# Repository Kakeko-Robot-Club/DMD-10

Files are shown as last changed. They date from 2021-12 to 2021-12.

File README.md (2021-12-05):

# DMD-10
ディスクリート部品によるDCブラシモータドライバ
## 目次
 - [仕様](#仕様)
 - [変更履歴](#変更履歴)
 - [発注](#発注)
 - [部品実装](#部品実装)
 - [使い方](#使い方)
## 仕様
### 絶対最大定格
| 項目 | 記号 | Max | 単位 | 
| --- | :---: | :---: | :--: |
| モータ出力電流(rms) | I<sub>OUT</sub> | 10 | A | 
| モータ出力電流(peak)  | I<sub>OUT_PEAK</sub> | 17 | A | 
| モータ電源電圧 | V<sub>DD</sub> | 0~16 | V | 
| ロジック入力電圧 | V<sub>IN</sub> | -6~23 | V | 
| 保存温度 | T<sub>S</sub> | -55~125 | ℃ | 
### 電気的特性・動作範囲
| 項目 | 記号 | Min | Typ. | Max | 単位 | コンディション | 
| --- | :---: | :-: | :--: | :-: | :--: | --- |
| モータ電源電圧 | V<sub>DD</sub>  | 6 | - | 16  | V | | 
| ロジック入力電圧(High)| V<sub>IH</sub>  | 3.6 | - | 20  | V | | 
| ロジック入力電圧(Low) | V<sub>IL</sub>  | 0 | - | 1.4 | V | | 
| ロジックPWM周波数 | f<sub>IN</sub>  | - | - | 27  | kHz | | 
| ロジック入力電流 | I<sub>IN</sub>  | - | 10 | - | mA | V<sub>IN</sub>=5V | 
### その他
| 項目 | 記号 | Min | Typ. | Max | 単位 | 備考 | 
| --- | :---: | :-: | :--: | :-: | :--: | --- |
| 基板サイズ(縦) | | - | 55 | - | mm | | 
| 基板サイズ(横) | | - | 60 | - | mm | | 
| 取り付け穴サイズ | | - | 3.2  | - | mm | M3ネジ用 | 
| 取り付け穴ピッチ(縦)  | | - | 46 | - | mm | | 
| 取り付け穴ピッチ(横)  | | - | 35 | - | mm | | 
### 図
 - [回路図](https://github.com/Kakeko-Robot-Club/DMD-10/blob/main/preview/schematic.pdf)
 - [基板外形図](https://github.com/Kakeko-Robot-Club/DMD-10/blob/main/preview/pcb.pdf)
## 変更履歴
 - Rev. A
	 - 初版(GitHubには未掲載)
 - Rev. B
	 - 部品リファレンス番号の振り直し
## 発注
 - 発注手順は[Elecrow](https://www.elecrow.com/pcb-manufacturing.html)に発注する際の手順を示しているため、その他の業者に発注する際は各業者の指示に従うこと。
 - 下の1～4の手順が難しい場合、このリポジトリの中にあるgerberフォルダの中のファイルを使用しても良い。ただし、手順1が行えないため注意。
 - 設定はKiCad v5系を元にしているため、その他のバージョンの場合は同等の設定にすること。
1. KiCadのPcbnewを用いて基板型番の下にある週番号を振り直す。
	 - この手順は省略できるが、製造時期を明確にするために行ったほうが良い。
2. Pcbnewから、ファイル→プロットと進み、出てきた画面で次のように設定をし、「製造ファイル出力」を押す。
	 - 出力フォーマット: ガーバー
	 - 出力ディレクトリ: gerberなど分かりやすいもの
	 - 含まれるレイヤ
		 - [x] F.Cu
		 - [x] B.Cu
		 - [x] F.SilkS
		 - [x] B.SilkS
		 - [x] F.Mask
		 - [x] B.Mask
		 - [x] Edge.Cuts
		 - その他はチェックを外す
	 - 全般オプション
		 - [x] フットプリントの定数をプロット
		 - [x] フットプリントのリファレンスをプロット
		 - [x] 基板外形レイヤーのデータを他のレイヤーから除外
		 - [x] シルクからパッドを除外
		 - その他はチェックを外す
		 - デフォルトの線幅: 0.1mm
	 - ガーバーオプション
		 - [x] Protelの拡張子を使用
		 - [x] シルクをレジストで抜く
		 - [x] ネットリスト属性を含む
		 - その他はチェックを外す
		 - 座標フォーマット: 4.6, 単位 mm
3. 製造ファイル出力ボタンの右の方にある、「ドリルファイルを生成...」ボタンから、次のように設定し、「ドリルファイルを生成」を押す。
	 - 出力フォルダ: 製造ファイル出力で設定したものと同じもの
	 - ドリルファイルフォーマット: Excellon
		 - チェックはすべて外す
		 - 長円穴ドリルモードは「routeコマンドを使用」にチェック
	 - マップファイルフォーマット: ガーバー
	 - ドリル原点: 絶対位置
	 - ドリル単位: mm
	 - ゼロの扱い: 後方ゼロ省略
4. 基板プロジェクトフォルダの中のフォルダ、または自分で設定したフォルダの中に生成したファイル群があるので、次のようにリネームする。
	 - DMD-10-Edge.Cuts.gm1のみ、拡張子がgmlに変わっているため注意

	| 元ファイル名         | リネーム後      | 
	| -------------------- | --------------- | 
	| DMD-10-B.Cu.gbl      | DMD-10.gbl      | 
	| DMD-10-B.Mask.gbs    | DMD-10.gbs      | 
	| DMD-10-B.SilkS.gbo   | DMD-10.gbo      | 
	| DMD-10-Edge.Cuts.gm1 | DMD-10.gml      | 
	| DMD-10-F.Cu.gtl      | DMD-10.gtl      | 
	| DMD-10-F.Mask.gts    | DMD-10.gts      | 
	| DMD-10-F.SilkS.gto   | DMD-10.gto      | 
	| DMD-10-NPTH.drl      | DMD-10-NPTH.txt | 
	| DMD-10-PTH.drl       | DMD-10-PTH.txt  | 
5. ファイルをZIPファイルに圧縮する。
6. [Elecrow](https://www.elecrow.com/pcb-manufacturing.html)にZIPファイルをアップロードし、次のような設定で発注する。
	 - Elecrowにログインしておくこと。

	| 項目                 | 設定             | 備考                                                   | 
	| -------------------- | :--------------: | ------------------------------------------------------ | 
	| Layer                | 2 layers         | 変更しないこと。                                       | 
	| Dimensions           | 60 x 55          | 変更しないこと。                                       | 
	| PCB Qty              | 必要枚数を設定   | 10枚までは安い。設定より少し多めに届くことが多い。     | 
	| Different PCB Design | 1                | 変更しないこと。                                       | 
	| PCB Thickness        | 1.6              | 薄くできるが非推奨。厚くすると高くなる。               | 
	| PCB Color            | 基板色を設定     | 一部の色は高い。                                       | 
	| Surface Finish       | HASL             | 鉛フリーや金メッキなども指定できるが高くなる。         | 
	| Castellated Hole     | No               | 変更しないこと。                                       | 
	| Copper Weight        | 1oz              | 2ozは基板銅箔が厚くなるが高くなる。                    | 
	| PCB Stencil          | No               | ステンシルは表面実装部品のリフロー半田に使うので不要。 | 
	| Production Time      | 4-7 working days | Rushなどにしてもそこまで早くならない。                 | 
	| Country              | Japan            | 配送先の国なので日本を選択。                           | 
	| Shipping Cost        | Sagawa           | 一番安いものを選んでおけばよい。                       | 
## 部品実装
 - 部品リスト
	| リファレンス | 部品                | 秋月電子                                                                                                                        | 代替品情報                                              | 
	| ------------ | ------------------- | ------------------------------------------------------------------------------------------------------------------------------- | ------------------------------------------------------- | 
	| D1～D4       | SBM1045VSS          | [I-15642](https://akizukidenshi.com/catalog/g/gI-15642/)                                                                        | I<sub>F</sub>>10A, V<sub>R</sub>>16V                    | 
	| J1～J4       | PCB-20(632F)        | [C-05115](https://akizukidenshi.com/catalog/g/gC-05115/)                                                                        | 15A以上流せるもの, できるだけ金属面積が広いもの         | 
	| J5           | PH-1x40RG(2)        | [C-01627](https://akizukidenshi.com/catalog/g/gC-01627/)                                                                        | 2.54mmピッチ, L字                                       | 
	| Q1, Q2       | MTA100N10KRI3       | 1個: [I-15846](https://akizukidenshi.com/catalog/g/gI-15846/)<br>10個: [I-15847](https://akizukidenshi.com/catalog/g/gI-15847/) | TO-251, Nch, I<sub>D</sub>>2A, V<sub>GS(th)</sub><4V    | 
	| Q3, Q5       | IRFU5505PBF         | [I-06021](https://akizukidenshi.com/catalog/g/gI-06021/)                                                                        | TO-251, Pch, I<sub>D</sub><-15A, V<sub>GS(th)</sub>>-4V | 
	| Q4, Q6       | IRLU3410PBF         | [I-06025](https://akizukidenshi.com/catalog/g/gI-06025/)                                                                        | TO-251, Nch, I<sub>D</sub>>15A, V<sub>GS(th)</sub><4V   | 
	| R1～R4       | 300Ωカーボン抵抗   | [R-07811](https://akizukidenshi.com/catalog/g/gR-07811/)                                                                        |                                                         | 
	| R5, R6       | 10kΩカーボン抵抗   | [R-07838](https://akizukidenshi.com/catalog/g/gR-07838/)                                                                        |                                                         | 
	| R7～R10      | 10Ωカーボン抵抗    | [R-07795](https://akizukidenshi.com/catalog/g/gR-07795/)                                                                        |                                                         | 
	| RN1          | 1kΩ 4素子集合抵抗  | [R-14225](https://akizukidenshi.com/catalog/g/gR-14225/)                                                                        |                                                         | 
	| RN2          | 10kΩ 4素子集合抵抗 | [R-11909](https://akizukidenshi.com/catalog/g/gR-11909/)                                                                        |                                                         | 
	| U1, U2       | UPC817CG-D04-T      | [I-16090](https://akizukidenshi.com/catalog/g/gI-16090/)                                                                        | PC817系フォトカプラ                                     | 
 - 注意点
	 - 抵抗やダイオードは縦取り付けになるよう、リードを曲げること。
	 - リードを曲げた抵抗を取り付ける際、基板から浮かないように取り付けること。
		 - 浮いている場合、抵抗が左右に曲がりやすくなり、ショートの原因になるため注意。
	 - 放熱のため、FETの頭の部分の半田付けは確実に行う。
		 - ランドが広いため、大出力の半田ごてを用いたほうが良い。
	 - ネジ端子はよく温めないと半田が流れないため、やけどに注意。
	 - 言うまでもなく、部品の向き・極性の間違い、定数の間違いに注意する。
## 使い方
1. 次のように接続する。
	| 端子      | リファレンス | 接続先             | 
	| --------- | ------------ | ------------------ | 
	| POWER IN  | J2           | モータ電源プラス   | 
	| POWER GND | J3           | モータ電源マイナス | 
	| MOTOR OUT | J1, J4       | DCブラシモータ     | 
	| IN1       | J5           | マイコン等出力端子 | 
	| IN2       | J5           | マイコン等出力端子 | 
	| GND       | J5           | マイコン等グランド | 
2. マイコン等から次の表に従い、IN1・IN2に信号を出力する。
	| IN2 | IN1 | J4  | J1  | モータ   | 
	| --- | --- | --- | --- | -------- | 
	| 0   | 0   | 1   | 1   | ブレーキ | 
	| 0   | 1   | 1   | 0   | 回転     | 
	| 1   | 0   | 0   | 1   | 逆回転   | 
	| 1   | 1   | 0   | 0   | ブレーキ | 
  
	*IN1・IN2欄は入力状態、J1・J4欄は出力状態、モータ欄は出力状態によるモータの状態を表す。  
	*IN1・IN2については0をV<sub>IL</sub>、1をV<sub>IH</sub>（PWM入力含む）に従うものとする。  
	*J1・J4については0を0V、1をV<sub>DD</sub>に従うものとする。

### 使用上の注意
 - 各端子をショートさせないこと。
 - 熱がこもるような狭い空間で使用しないこと。
 - 定格を超えての使用をしないこと。
 - 異常発熱がある場合は使用しないこと。

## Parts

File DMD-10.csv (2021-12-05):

Reference | Value | Footprint | Datasheet
J3 | Conn_01x04 | Connector_PinHeader_2.54mm:PinHeader_1x04_P2.54mm_Horizontal | ~
U1 | PC817 | Package_DIP:DIP-4_W7.62mm | http://www.soselectronic.cz/a_info/resource/d/pc817.pdf
U2 | PC817 | Package_DIP:DIP-4_W7.62mm | http://www.soselectronic.cz/a_info/resource/d/pc817.pdf
R1 | 380 | Resistor_THT:R_Axial_DIN0204_L3.6mm_D1.6mm_P2.54mm_Vertical | ~
R2 | 380 | Resistor_THT:R_Axial_DIN0204_L3.6mm_D1.6mm_P2.54mm_Vertical | ~
R5 | 300 | Resistor_THT:R_Axial_DIN0204_L3.6mm_D1.6mm_P2.54mm_Vertical | ~
R6 | 300 | Resistor_THT:R_Axial_DIN0204_L3.6mm_D1.6mm_P2.54mm_Vertical | ~
Q1 | MTA100N10KRI3 | Package_TO_SOT_THT:TO-251-3-1EP_Horizontal_TabDown | ~
Q2 | MTA100N10KRI3 | Package_TO_SOT_THT:TO-251-3-1EP_Horizontal_TabDown | ~
R7 | 10k | Resistor_THT:R_Axial_DIN0204_L3.6mm_D1.6mm_P2.54mm_Vertical | ~
R8 | 10k | Resistor_THT:R_Axial_DIN0204_L3.6mm_D1.6mm_P2.54mm_Vertical | ~
Q4 | IRLU3410PBF | Package_TO_SOT_THT:TO-251-3-1EP_Horizontal_TabDown | ~
Q6 | IRLU3410PBF | Package_TO_SOT_THT:TO-251-3-1EP_Horizontal_TabDown | ~
R11 | 10 | Resistor_THT:R_Axial_DIN0204_L3.6mm_D1.6mm_P2.54mm_Vertical | ~
R12 | 10 | Resistor_THT:R_Axial_DIN0204_L3.6mm_D1.6mm_P2.54mm_Vertical | ~
Q3 | IRFU5505PBF | Package_TO_SOT_THT:TO-251-3-1EP_Horizontal_TabDown | ~
Q5 | IRFU5505PBF | Package_TO_SOT_THT:TO-251-3-1EP_Horizontal_TabDown | ~
R13 | 10 | Resistor_THT:R_Axial_DIN0204_L3.6mm_D1.6mm_P2.54mm_Vertical | ~
R14 | 10 | Resistor_THT:R_Axial_DIN0204_L3.6mm_D1.6mm_P2.54mm_Vertical | ~
D1 | SBM1045VSS | Diode_THT:D_DO-201AD_P3.81mm_Vertical_AnodeUp | ~
D2 | SBM1045VSS | Diode_THT:D_DO-201AD_P3.81mm_Vertical_AnodeUp | ~
D3 | SBM1045VSS | Diode_THT:D_DO-201AD_P3.81mm_Vertical_AnodeUp | ~
D4 | SBM1045VSS | Diode_THT:D_DO-201AD_P3.81mm_Vertical_AnodeUp | ~
J4 | Conn_01x01 | PCB-20(632)F:DIP-6_W7.62mm | ~
J5 | Conn_01x01 | PCB-20(632)F:DIP-6_W7.62mm | ~
J2 | Conn_01x01 | PCB-20(632)F:DIP-6_W7.62mm | ~
J1 | Conn_01x01 | PCB-20(632)F:DIP-6_W7.62mm | ~
RN1 | 10k | Resistor_THT:R_Array_SIP5 | http://www.vishay.com/docs/31509/csc.pdf
RN2 | 1k | Resistor_THT:R_Array_SIP5 | http://www.vishay.com/docs/31509/csc.pdf

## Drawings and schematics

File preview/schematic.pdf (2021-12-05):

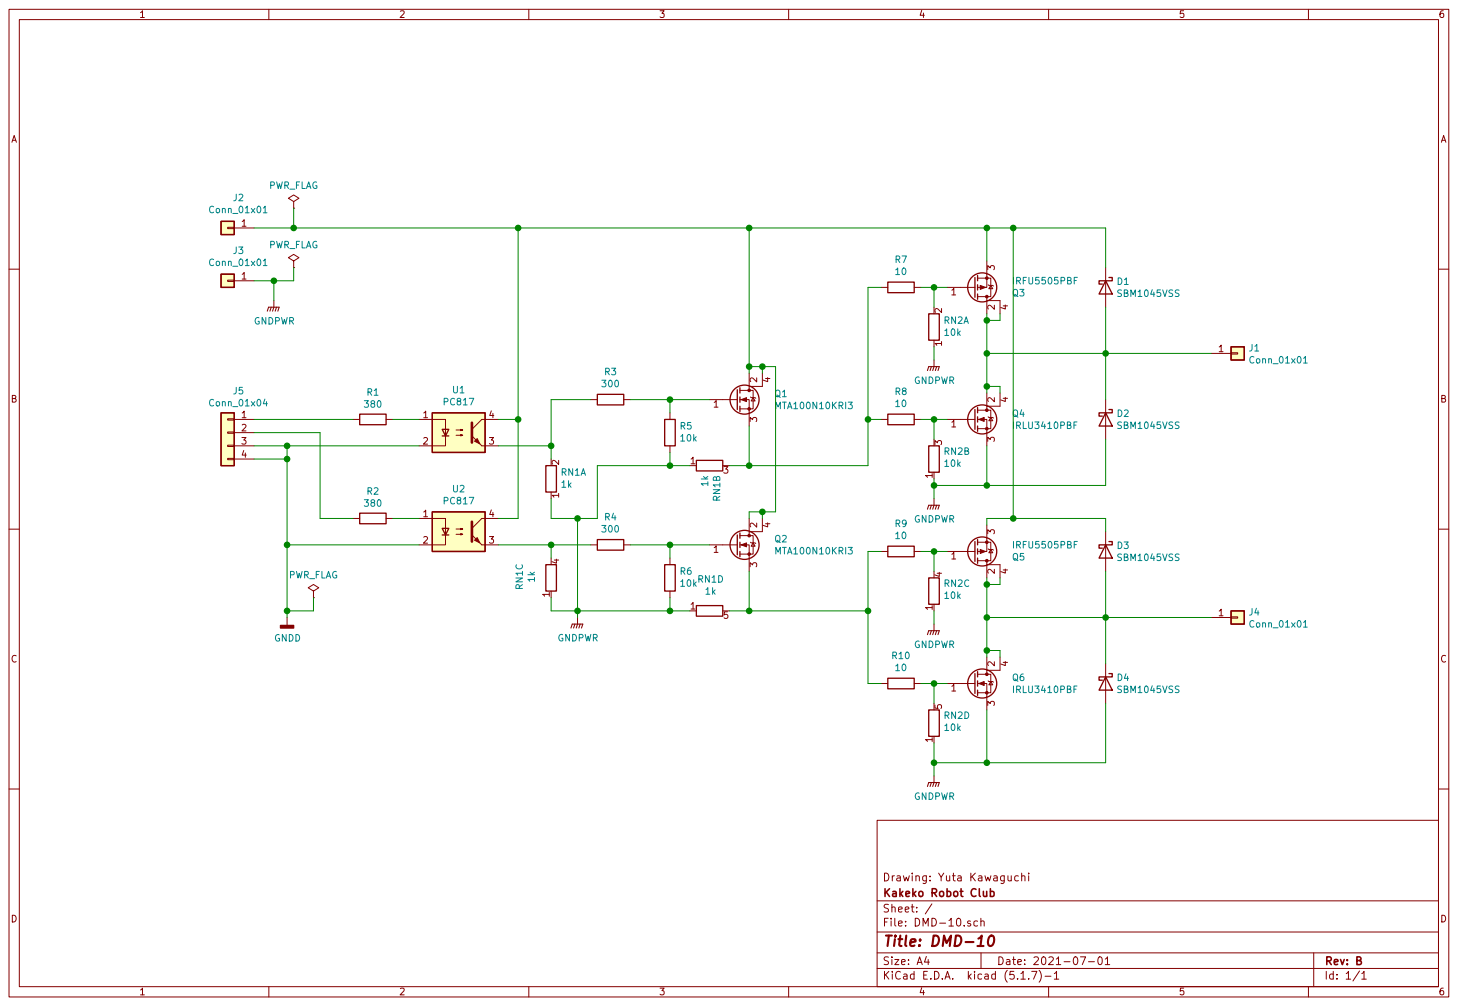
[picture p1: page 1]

File: DMD-10.sch Sheet: / Kakeko Robot Club Drawing: Yuta Kawaguchi

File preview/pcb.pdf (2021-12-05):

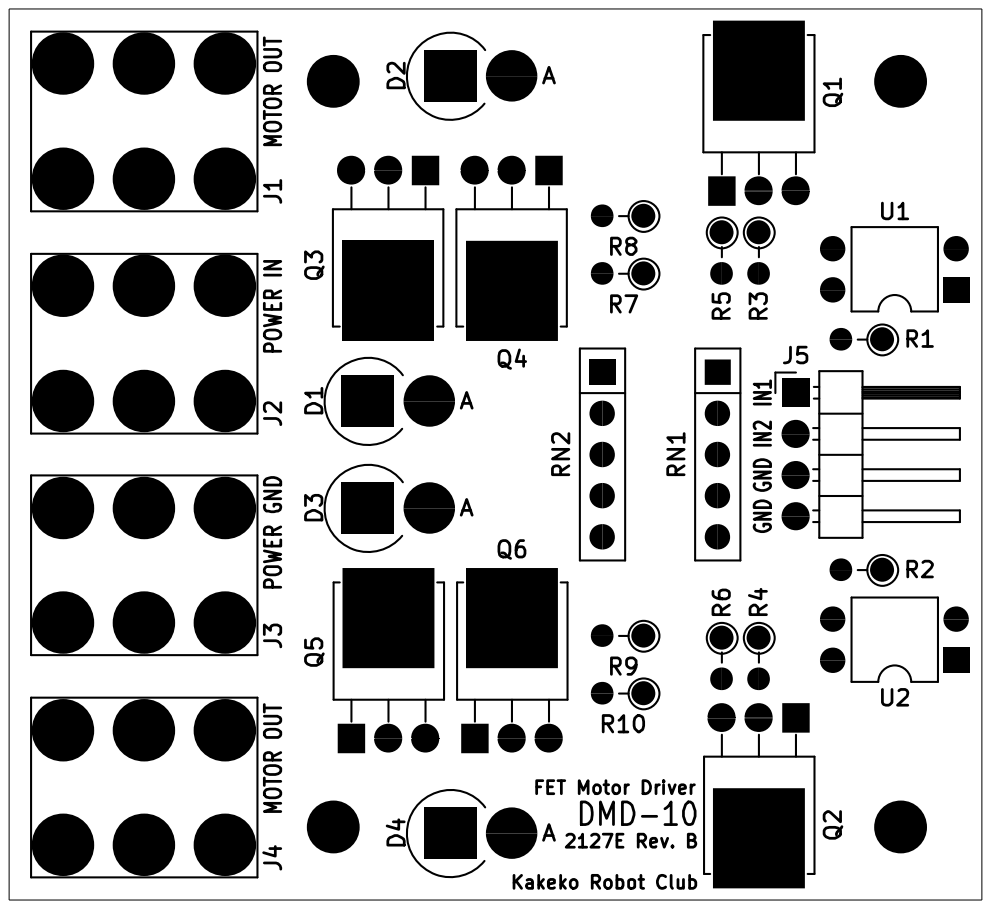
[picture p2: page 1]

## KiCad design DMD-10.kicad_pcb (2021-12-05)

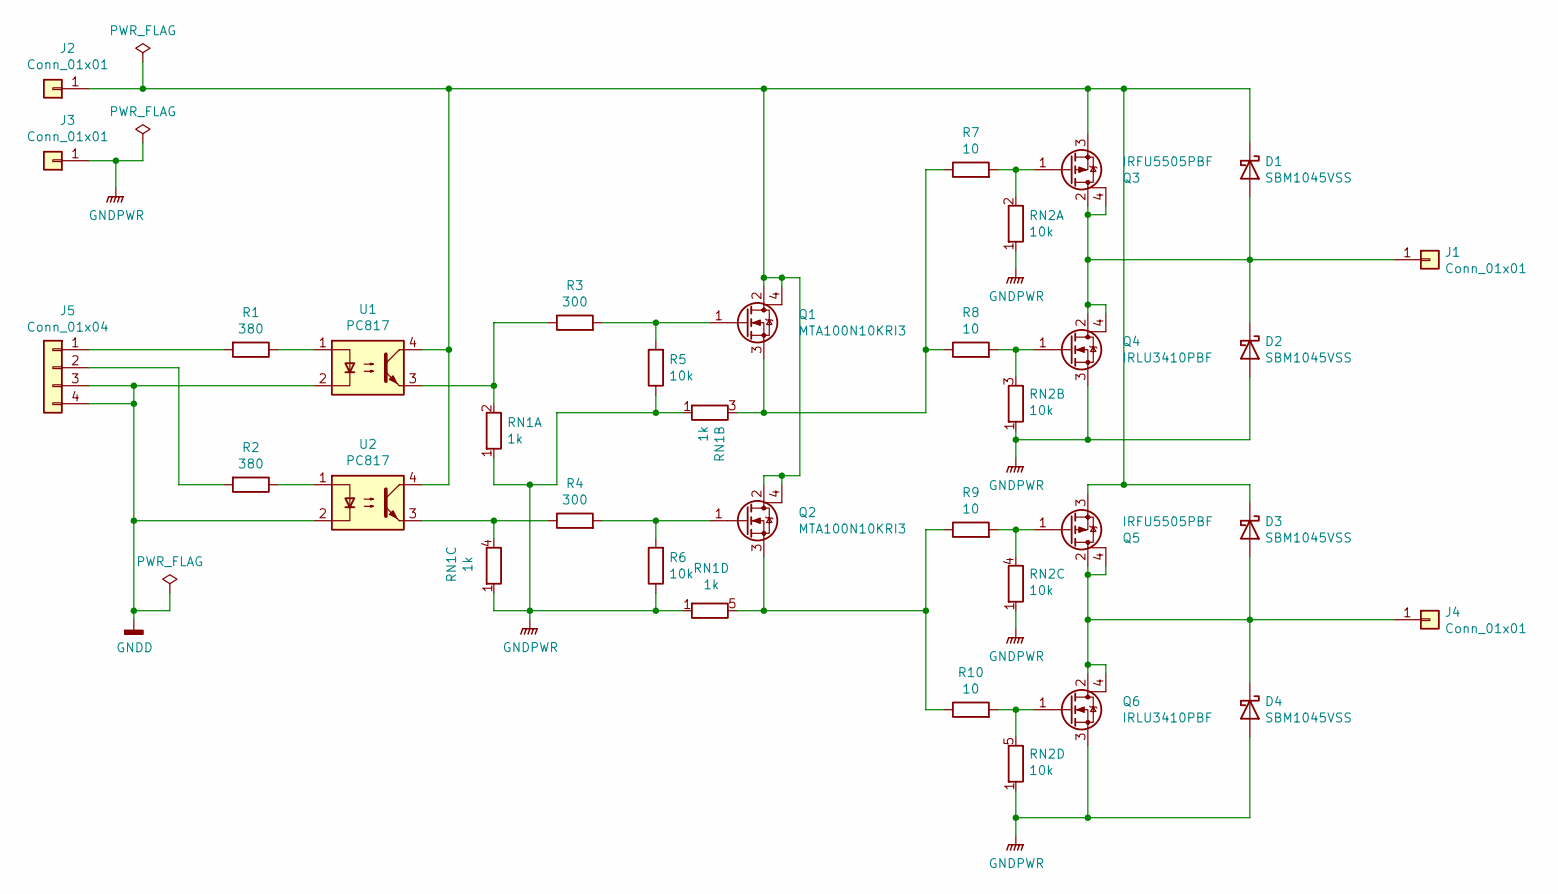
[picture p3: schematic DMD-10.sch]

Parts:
D1, D2, D3, D4: SBM1045VSS; D_DO-201AD_P3.81mm_Vertical_AnodeUp
J1, J2, J3, J4: Conn_01x01; DIP-6_W7.62mm
J5: Conn_01x04; PinHeader_1x04_P2.54mm_Horizontal
Q1, Q2: MTA100N10KRI3; TO-251-3-1EP_Horizontal_TabDown
Q3, Q5: IRFU5505PBF; TO-251-3-1EP_Horizontal_TabDown
Q4, Q6: IRLU3410PBF; TO-251-3-1EP_Horizontal_TabDown
R1, R2: 380; R_Axial_DIN0204_L3.6mm_D1.6mm_P2.54mm_Vertical
R3, R4: 300; R_Axial_DIN0204_L3.6mm_D1.6mm_P2.54mm_Vertical
R5, R6: 10k; R_Axial_DIN0204_L3.6mm_D1.6mm_P2.54mm_Vertical
R7, R8, R9, R10: 10; R_Axial_DIN0204_L3.6mm_D1.6mm_P2.54mm_Vertical
RN1: 1k; R_Array_SIP5
RN2: 10k; R_Array_SIP5
U1, U2: PC817; DIP-4_W7.62mm

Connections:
GNDD: J5.3, J5.4, U1.2, U2.2
GNDPWR: D2.2 (A), D4.2 (A), J3.1, Q4.3 (S), Q6.3 (S), R5.1, R6.1, RN1.1 (R1.1), RN2.1 (R1.1)
unnamed: D1.1 (K), D3.1 (K), J2.1, Q1.2 (D), Q1.4 (D), Q2.2 (D), Q2.4 (D), Q3.3 (S), Q5.3 (S), U1.4, U2.4
unnamed: D1.2 (A), D2.1 (K), J1.1, Q3.2 (D), Q3.4 (D), Q4.2 (D), Q4.4 (D)
unnamed: D3.2 (A), D4.1 (K), J4.1, Q5.2 (D), Q5.4 (D), Q6.2 (D), Q6.4 (D)
unnamed: J5.1, R1.2
unnamed: J5.2, R2.2
unnamed: Q1.1 (G), R3.2, R5.2
unnamed: Q1.3 (S), R7.1, R8.1, RN1.3 (R2.2)
unnamed: Q2.1 (G), R4.2, R6.2
unnamed: Q2.3 (S), R9.1, R10.1, RN1.5 (R4.2)
unnamed: Q3.1 (G), R7.2, RN2.2 (R1.2)
unnamed: Q4.1 (G), R8.2, RN2.3 (R2.2)
unnamed: Q5.1 (G), R9.2, RN2.4 (R3.2)
unnamed: Q6.1 (G), R10.2, RN2.5 (R4.2)
unnamed: R1.1, U1.1
unnamed: R2.1, U2.1
unnamed: R3.1, RN1.2 (R1.2), U1.3
unnamed: R4.1, RN1.4 (R3.2), U2.3

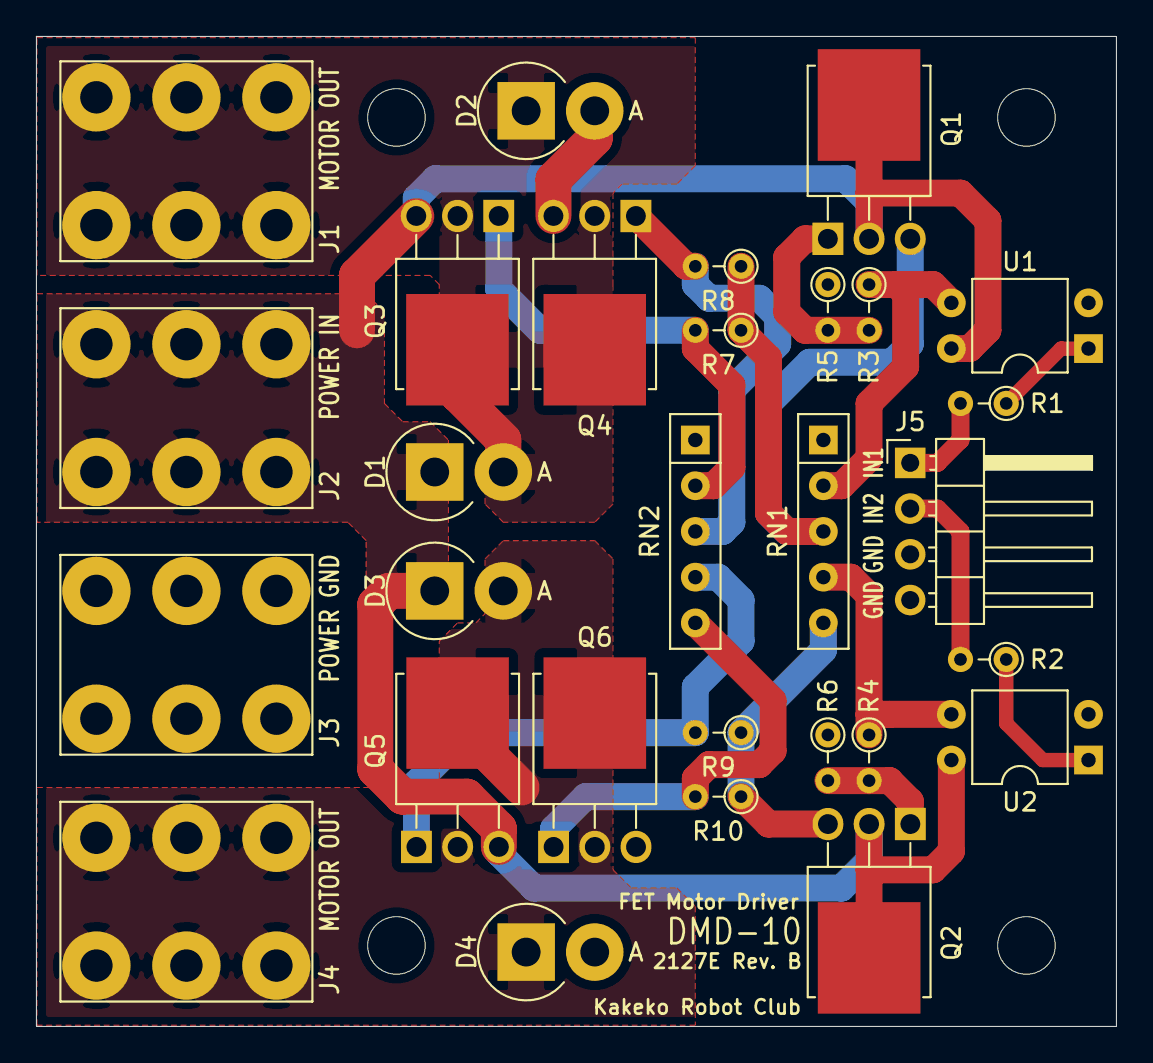
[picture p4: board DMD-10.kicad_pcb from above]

Board: 2 copper layers, 60.0 x 55.0 mm, 29 parts (0 on the bottom side), 19 nets.
